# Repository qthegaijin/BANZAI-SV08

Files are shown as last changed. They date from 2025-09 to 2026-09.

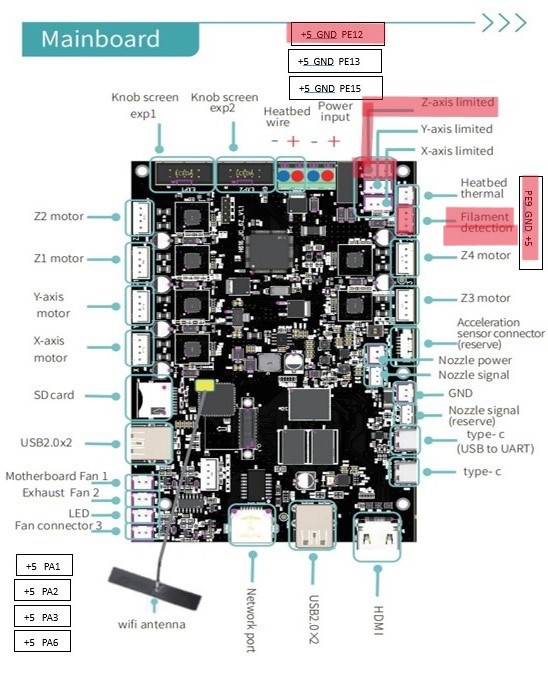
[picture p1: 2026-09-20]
Pinouts/Sovol SV08 MCU_PIN_definition_2 (1).jpg

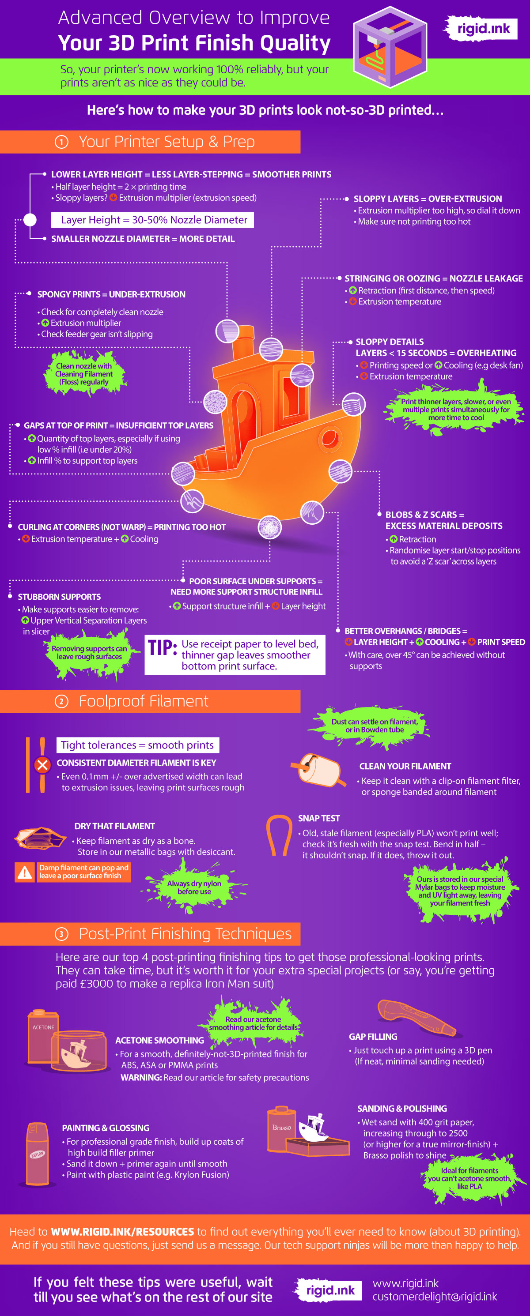
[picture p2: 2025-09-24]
Calibration STLs/Benchy Guide.jpg

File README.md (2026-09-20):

# BANZAI-SV08
Modifications, Configs and Orca Slicer Profiles for the Sovol SV08 3D Printer
<br>
<br>
Model: Sovol SV08 - https://www.sovol3d.com/products/sovol-sv08-3d-printer
<br>
Firmware: Klipper - Mainline - https://github.com/Rappetor/Sovol-SV08-Mainline
<br>
Probe - EddyDuo running eddy-ng - https://github.com/vvuk/eddy-ng/wiki
<br>
KlipperExpander - https://github.com/VoronDesign/Voron-Hardware/tree/master/Klipper_Expander
<br>
Toolhead Cover - Custom Version Coming Soon
<br>
Tophat - https://www.printables.com/model/1392873-sv08-top-hat-double-top-hat-enclosed-for-mmus
<br>
Feet/Risers - https://www.printables.com/model/1041899-sovol-sv08-feet-v4
<br>
Door Stop - https://www.printables.com/model/1003732-sv08-door-stop
<br>
Spool Holder Relocation - https://www.printables.com/model/928589-sovol-sv08-side-mount-spool-holder-remix
<br>
SV08 Gantry Belt Fix - https://www.printables.com/model/1154812-sovol-sv08-side-slide-carriage-make-parallel-to-th
<br>
<br>
Custom SV08 Configs Description -
<br>
eddy-ng.cfg - working config for eddy-ng with updated homing and QGL.
<br>
heatsoak.cfg - variable heatsoak macro
<br>
klipperExpander.cfg - expander board config for Chamber Thermistor
<br>
led-control.cfg - controls toolhead neopixel LED
<br>
printer.cfg - main printer config - use as a reference
<br>
sovol-macros.cfg - updated mainline SV08 Macros
<br>
sovol-stock-purge.cfg - only the purge line macro from the stock sovol setup instead of using KAMP.
<br>
Orbiter2_SmartSensor.cfg - Orbiter Smart Filament Sensor setup for the SV08 on pins PE9 and PE12
<br>
<br>
Custom BANZAI Mods - 
<br>
BANZAI MCU Fan Adapter - Replaces the stock metal sheet cover with a small footprint fan holder. Requres 2 or 4x M3x5mm Heatset Inserts.
<br>

<br>
<br>
BANZAI Bed Plate Mod - Replaces the stock plastic bed plate for use with the SV08 Taco Bed Mod without needing to glue any washers: https://github.com/Wrath669/SV08BedTension/blob/main/README.md. Requires 9 M4x8mm Heatset Inserts.
<br>

<br>

<br>
<br>
Calibration STLs - 
<br>
Suggested Tuning Tutorial Video: https://www.youtube.com/watch?v=trXzdfWCHI8
<br>
Calibration Cube + Key Measuerments Guide - Cube with holes and angled features to measure dimensional accuracy
<br>
Firebolt Calibration - 2A Feature calibration cube "IYKYK"
<br>
Flow Calibration (Depreciated Method, use Built In Orca Calibration Tools instead) - Filament flow calibration square for 0.4MM Nozzles. Print with filament flow ratio at 1.00 to start then measure the walls of the print with calipers. Use the equation 1.20/(Measured Value)*(Flow Rate) to find the desired rate. Repeat steps with new settings applied and remeasure. If walls are > or < 1.20mm redo the equation and rerun the test until you are in the 1.19-1.21mm wall range. 
<br>
<br>
Orca Slicer 2.3.1 Settings -
<br>
<br>
Printer Settings
<br>
SV08-I
<br>
SV08-M
<br>
SV08-E
<br>
SV08-MO
<br>
<br>

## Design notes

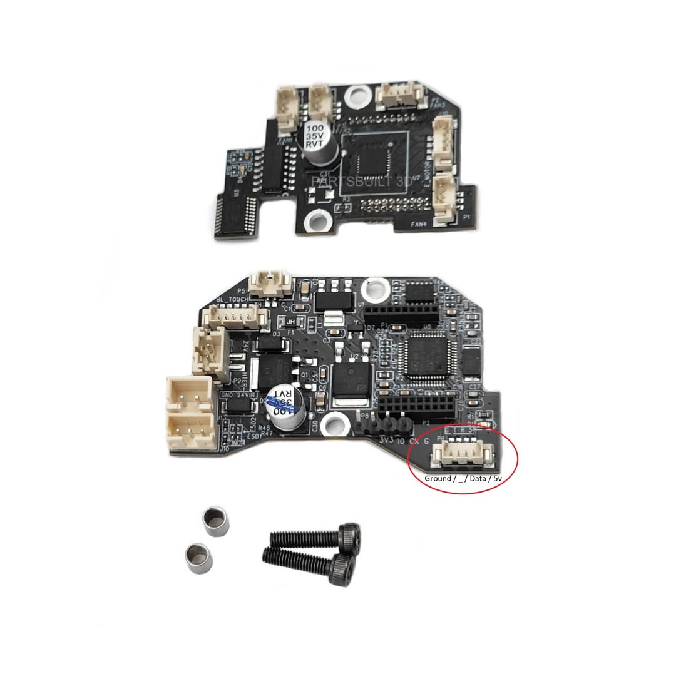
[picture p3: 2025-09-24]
Pinouts/SV08 Toolhead Neo-Pixel Pinout.jpg

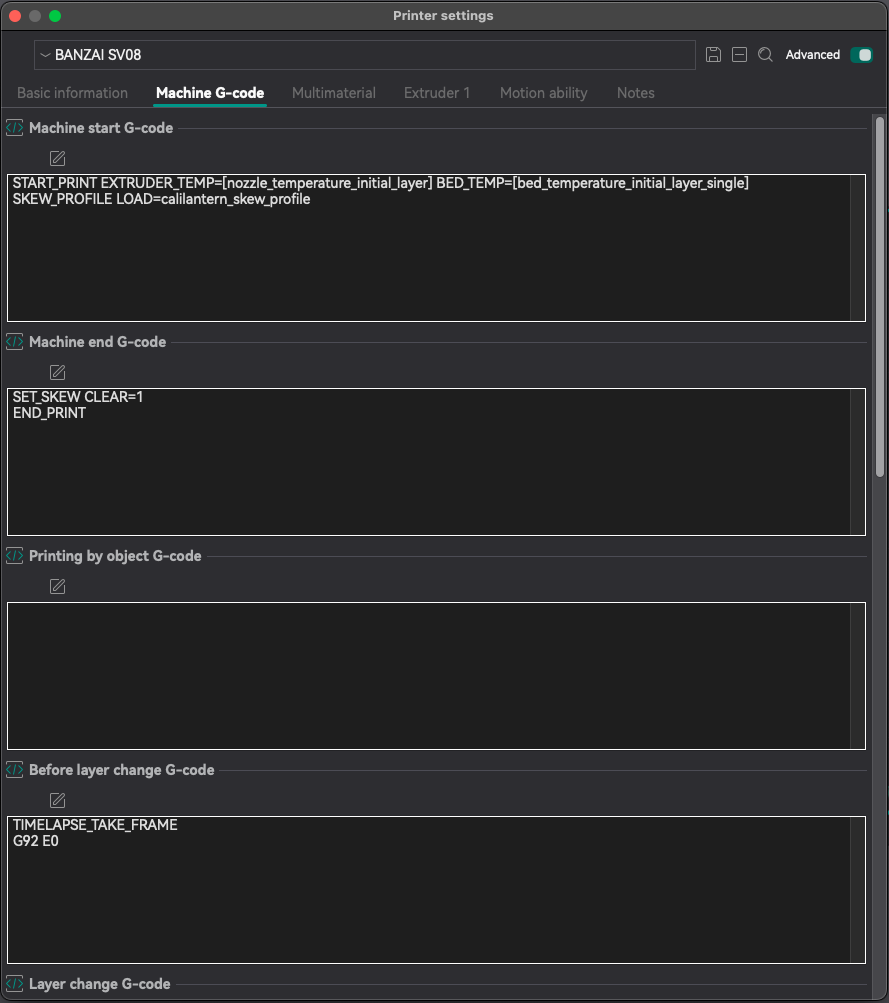
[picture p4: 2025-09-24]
BANZAI SV08 Slicer Images/SV08-M.png

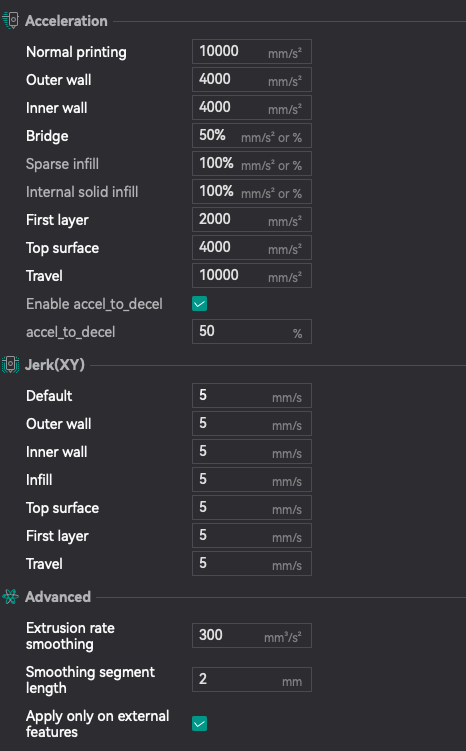
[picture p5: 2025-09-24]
BANZAI SV08 Slicer Images/SP2.png

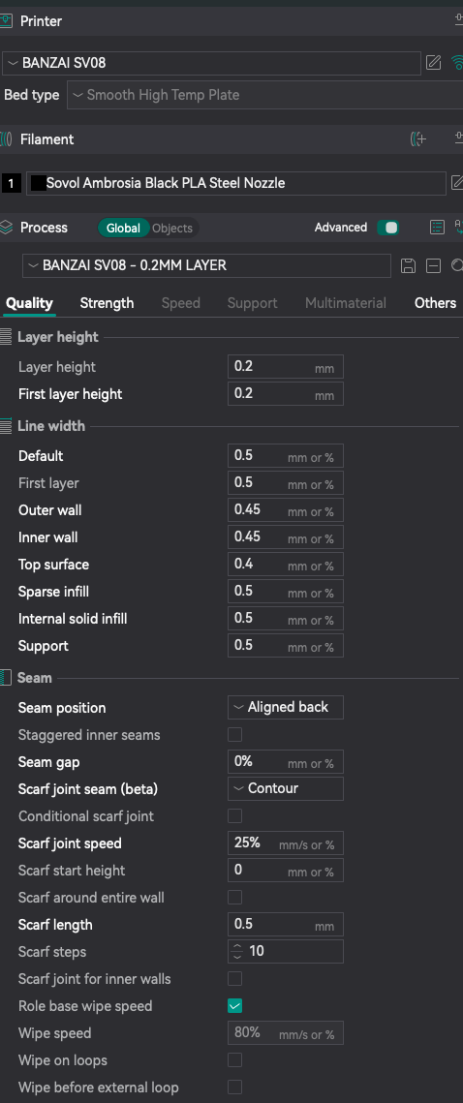
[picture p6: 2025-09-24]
BANZAI SV08 Slicer Images/Q1.png

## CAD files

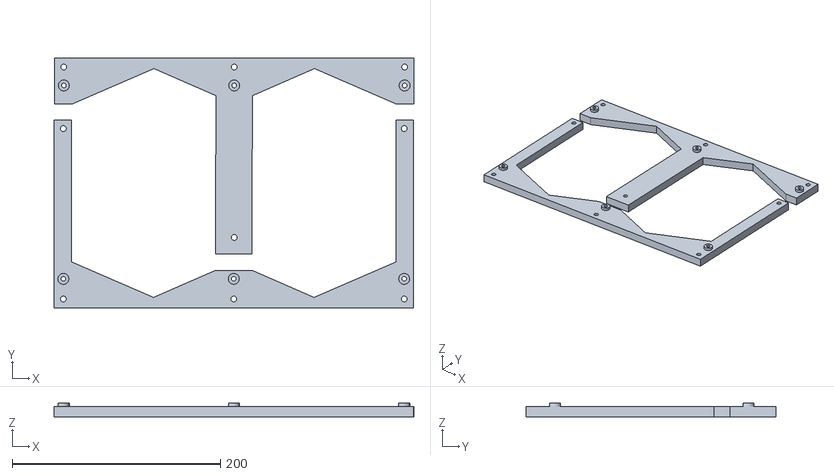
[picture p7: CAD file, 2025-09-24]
BANZAI Custom SV08 Parts/SV08 BANZAI Bed Plate Mod.stl
345.4 x 239.6 x 13.3

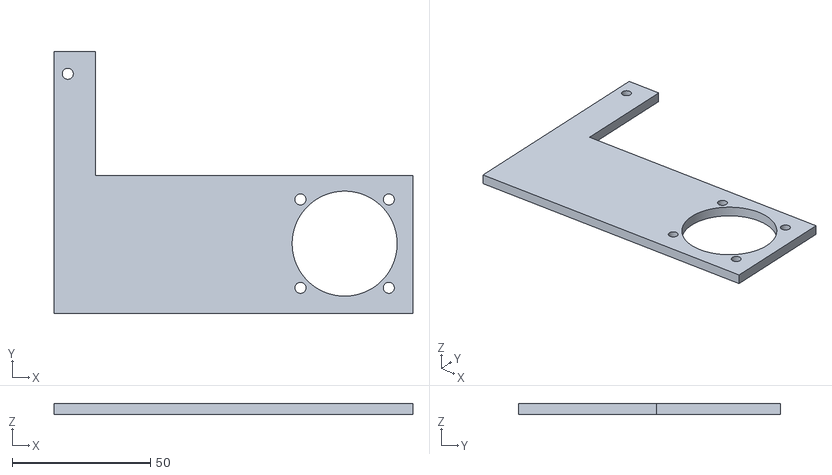
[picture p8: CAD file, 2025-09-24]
BANZAI Custom SV08 Parts/SV08 BANZAI MCU Fan Holder.stl
130.0 x 95.0 x 4.00

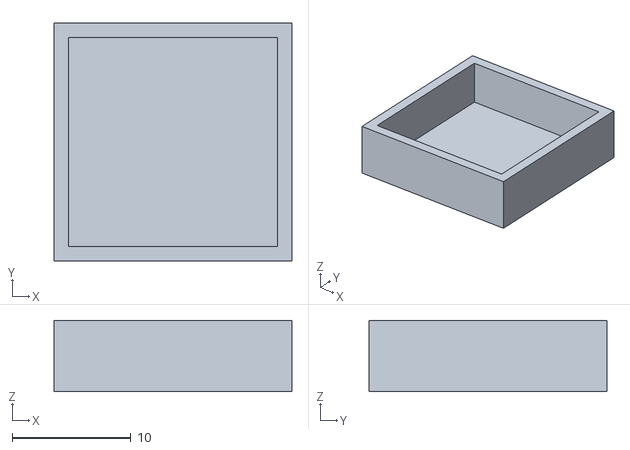
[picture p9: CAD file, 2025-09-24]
Calibration STLs/Flow_Calibration.STL
20.0 x 20.0 x 6.00

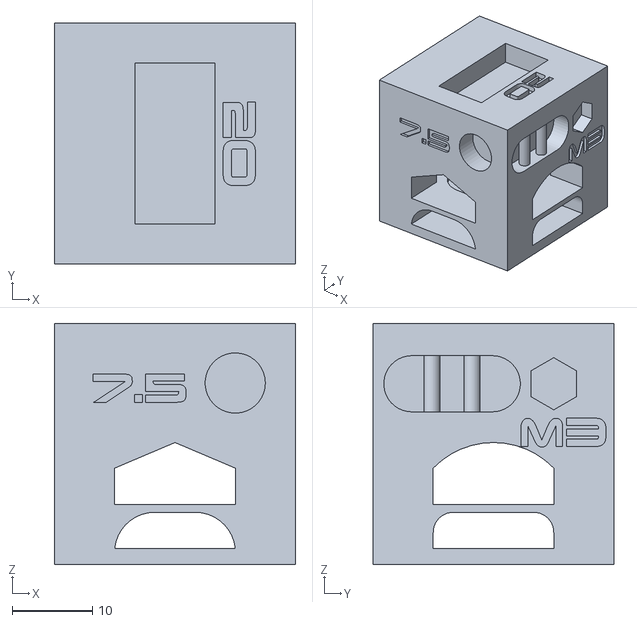
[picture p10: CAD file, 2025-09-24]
Calibration STLs/Calibration_Cube.STL
30.0 x 30.0 x 30.0

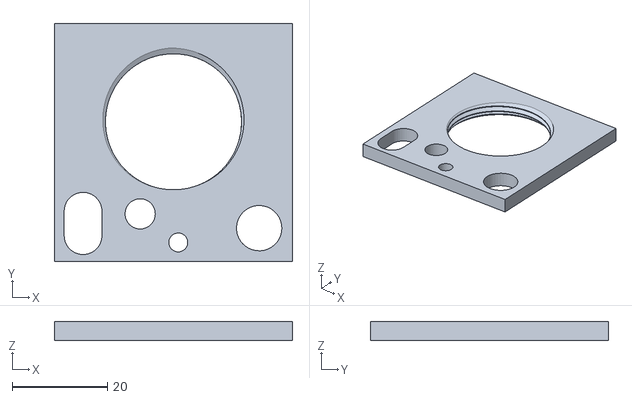
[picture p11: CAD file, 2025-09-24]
Calibration STLs/Firebolt_Calibration_Test.STL
50.0 x 50.0 x 4.00

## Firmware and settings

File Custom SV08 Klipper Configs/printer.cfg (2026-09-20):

[include mainsail.cfg]
[include sovol-macros.cfg]
[include timelapse.cfg] # DONT FORGET TO INSTALL THE TIMELAPSE PLUGIN
[include sovol-stock-purge.cfg]
[include heatsoak.cfg]
[include led-control.cfg]
[include Orbiter2_SmartSensor.cfg]

# PLEASE UNCOMMENT THE FILE THAT BEST FITS YOUR CONFIGURATION

# IF YOU ARE USING THE SCREEN THAT COMES WITH THE SV08
[include options/lcd/*.cfg]

# IF YOU HAVE KLIPPERSCREEN / AN HDMI DISPLAY ATTACHED TO YOUR PRINTER
# [include options/hdmi/*.cfg]

# If you are using the stock probe, keep the following lines as-is.
# If you have an Eddy probe, comment the first and uncomment the second
# [include stock_probe.cfg]
[include eddy-ng.cfg]

# If you are running a Klipper Expander Board
[include klipperExpander.cfg]

# If you will run KAMP Adaptive Purge/Mesh (DOES NOT WORK WITH EDDY_NG)
# [include KAMP_Settings.cfg]


[mcu]
serial: /dev/serial/by-id/usb-Klipper_stm32f103xe_
restart_method: command     

[mcu extra_mcu]
serial: /dev/serial/by-id/usb-Klipper_stm32f103xe_
restart_method: command      

[virtual_sdcard]
path: ~/printer_data/gcodes
on_error_gcode: CANCEL_PRINT

[printer]
kinematics: corexy           
max_velocity: 700            
max_accel: 20000             
#max_accel_to_decel: 10000 # deprecated
minimum_cruise_ratio: 0.5
max_z_velocity: 20
max_z_accel: 500
square_corner_velocity: 6.79

[stepper_x]
step_pin: PE2
dir_pin: !PE0
enable_pin: !PE3
rotation_distance: 40         
microsteps: 64                
full_steps_per_rotation:200   
endstop_pin: tmc2209_stepper_x: virtual_endstop              
position_min: 0 #-1               
position_endstop: 355         
position_max: 355             
homing_speed: 50              
homing_retract_dist: 0        
homing_positive_dir: True     
#--------------------------------------------------------------------
[tmc2209 stepper_x]
uart_pin: PE1
interpolate: False #True             
run_current: 1.1 #1.5
#hold_current: 1.061 #1.5            
sense_resistor: 0.150         
#stealthchop_threshold: 0      
uart_address:3
driver_sgthrs: 75 #65
diag_pin: PE15
driver_TBL: 1
driver_TOFF: 3
driver_HSTRT: 7
driver_HEND: 5

[stepper_y]
step_pin: PB8
dir_pin: !PB6
enable_pin: !PB9
rotation_distance: 40         
microsteps: 64                
full_steps_per_rotation:200   
endstop_pin: tmc2209_stepper_y: virtual_endstop              
position_min: 0 #-1               
position_endstop: 362         
position_max: 362            
homing_speed: 50              
homing_retract_dist: 0        
homing_positive_dir: true     
#--------------------------------------------------------------------
[tmc2209 stepper_y]
uart_pin: PB7
interpolate: False #True             
run_current: 1.1 #1.5
#hold_current: 1.061 #1.5             
sense_resistor: 0.150         
#stealthchop_threshold: 0      
uart_address:3
driver_sgthrs: 85 #75 #65
diag_pin: PE13
driver_TBL: 1
driver_TOFF: 3
driver_HSTRT: 7
driver_HEND: 5

[stepper_z] #motherboard：Z3 
step_pin:PC0    
dir_pin:PE5    
enable_pin:!PC1    
rotation_distance: 40         
gear_ratio: 80:12             
microsteps: 16
endstop_pin: probe:z_virtual_endstop           
position_max: 347             
position_min: -5              
#position_endstop: 0
homing_speed: 15.0
homing_retract_dist: 5.0
homing_retract_speed: 15.0
second_homing_speed: 10.0
#--------------------------------------------------------------------
[tmc2209 stepper_z]
uart_pin: PE6 
interpolate: false #true             
run_current: 0.566 #0.58          
#hold_current: 0.566 #0.58         
sense_resistor: 0.150       
stealthchop_threshold: 999999 
uart_address:3
#driver_TBL: 1
#driver_TOFF: 3
#driver_HSTRT: 0
#driver_HEND: 2

[stepper_z1] ##motherboard：Z1
step_pin:PD3  
dir_pin:!PD1 
enable_pin:!PD4 
rotation_distance: 40         
gear_ratio: 80:12            
microsteps: 64 #16        
#--------------------------------------------------------------------
[tmc2209 stepper_z1]
uart_pin:PD2  
interpolate: false #true             
run_current: 0.566 #0.58          
#hold_current: 0.566 #0.58         
sense_resistor: 0.150  
stealthchop_threshold: 999999 
uart_address:3
#driver_TBL: 1
#driver_TOFF: 3
#driver_HSTRT: 0
#driver_HEND: 2

[stepper_z2] ##motherboard：Z2
step_pin:PD7
dir_pin:PD5   
enable_pin:!PB5
rotation_distance: 40         
gear_ratio: 80:12             
microsteps: 64 #16          
#--------------------------------------------------------------------
[tmc2209 stepper_z2]
uart_pin:PD6  
interpolate: false #true             
run_current: 0.566 #0.58          
#hold_current: 0.566 #0.58         
sense_resistor: 0.150   
stealthchop_threshold: 999999 
uart_address:3
#driver_TBL: 1
#driver_TOFF: 3
#driver_HSTRT: 0
#driver_HEND: 2

[stepper_z3] ##motherboard：Z4
step_pin:PD11 
dir_pin:!PD9 
enable_pin:!PD12   
rotation_distance: 40         
gear_ratio: 80:12             
microsteps: 64 #16       
#--------------------------------------------------------------------
[tmc2209 stepper_z3]
uart_pin:PD10    
interpolate: false #true             
run_current: 0.566 #0.58          
#hold_current: 0.566 #0.58         
sense_resistor: 0.150
stealthchop_threshold: 999999 
uart_address:3
#driver_TBL: 1
#driver_TOFF: 3
#driver_HSTRT: 0
#driver_HEND: 2

[thermistor my_thermistor_e]
temperature1:25
resistance1:110000
temperature2:100
resistance2:7008
temperature3:220
resistance3:435

[extruder]
step_pin: extra_mcu:PA8   
dir_pin: extra_mcu:PB8    
enable_pin:!extra_mcu: PB11   
rotation_distance: 4.69 #6.5 
microsteps: 32 #16                
full_steps_per_rotation: 200 
nozzle_diameter: 0.400        
filament_diameter: 1.75  
max_extrude_only_distance: 500 #150
max_extrude_only_velocity: 120
heater_pin:extra_mcu:PB9  
sensor_type:my_thermistor_e  
pullup_resistor: 11500
sensor_pin: extra_mcu:PA5  
min_temp: 5                  
max_temp: 310                 
max_power: 1.0                
min_extrude_temp: 5
#control : pid
#pid_kp : 33.838
#pid_ki : 5.223
#pid_kd : 47.752
pressure_advance: 0.025       
pressure_advance_smooth_time: 0.035    
#--------------------------------------------------------------------
[tmc2209 extruder]
uart_pin: extra_mcu:PB10  
interpolate: False #True             
run_current: 0.8
#hold_current: #0.8            
uart_address:3
sense_resistor: 0.110 #0.150
stealthchop_threshold: 0
driver_TBL: 0
driver_TOFF: 4
driver_HSTRT: 7
driver_HEND: 6       

[verify_heater extruder]      
max_error: 120                
check_gain_time:30           
hysteresis: 5                
heating_gain: 2               

# [filament_switch_sensor filament_sensor]
# pause_on_runout: True
# event_delay: 3.0
# pause_delay: 0.5
# switch_pin: PE9

#[thermistor my_thermistor]
#temperature1:25
#resistance1:100000
#temperature2:50
#resistance2:18085.4
#temperature3:100
#resistance3:5362.6

[thermistor my_thermistor]
temperature1:25
resistance1:100000
temperature2:75
resistance2:8856.69
temperature3:125
resistance3:3637.10

[heater_bed]
heater_pin:PA0
sensor_type: my_thermistor  
sensor_pin: PC5
max_power: 1.0               
min_temp: 5                  
max_temp: 125                
#control : pid
#pid_kp : 73.571
#pid_ki : 1.820
#pid_kd : 783.849

[verify_heater heater_bed]      
max_error: 120                
check_gain_time:40           
hysteresis: 5                
heating_gain: 2 

# [probe_pressure]
# pin: ^!PE12     
# x_offset: 0                  
# y_offset: 0
# z_offset : 0
# speed: 1.0

[quad_gantry_level]          
gantry_corners:              
	-60,-10
	410,420
points:
	36,10
	36,320
	346,320
	346,10
speed: 300                   
horizontal_move_z: 5       
retry_tolerance: 0.05      
retries: 10                  
max_adjust: 30   

[multi_pin print_cooling_fan_pins]
pins: extra_mcu:PA7, extra_mcu:PB1

# print/part cooling fan
[fan]
pin: multi_pin:print_cooling_fan_pins
max_power: 1.0

[fan_generic exhaust_fan] # exhaust fan
pin: PA2
max_power: 1.0

# MCU fan, aka noisy boi, is now only enabled when using steppers, extruder, heatbed; 5min timeout
[controller_fan MCU_fan]
pin: PA1
max_power: 1
kick_start_time: 0.5
fan_speed: 1
idle_timeout: 300
heater: extruder, heater_bed
stepper: stepper_x, stepper_y
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

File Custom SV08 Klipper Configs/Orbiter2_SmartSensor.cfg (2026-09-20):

#################################################################################################################
################################# Orbiter Sensor CONFIGURATION ##################################################
#################################################################################################################

#config file version v3.0.02
#release date: 22.12.2023

# PAUSE and RESUME macros are defined at the end of this config file.
# If you prefer using your own p[lease delete them, otherwise define parking position below.

#################################################################################################################
################################# CHANGE HERE MACRO CONFIGURABLES################################################
#################################################################################################################

[gcode_macro _SENSOR_VARIABLES]         # change here macro configurables, enable disable functions!*************************
variable_filament_load_temp     :260    # temperature to heat up hotend for filament loading, default is 235
variable_filament_unload_temp   :260    # temperature to heat up hotend for filament un-loading, default is 185
variable_filament_load_min_temp :190    # minimum hotend set temperature allowed in filament load macro, default is 190
variable_nozzle_purge_length    :100    # filament extrude amount during load sequenc, hotend purge from old filament, default is 200
variable_nozzle_purge_speed     :450    # filament extrude speed in mm/min adjust this value lower if flow is too high and extruder skips during loading, default is 300
variable_unload_distance        :65     # filament retract distance for unload procedure. this length shall be long enough to extract the filament above the drive gears
variable_disable_autoload       :False  # disable filament autoload feature by setting this variable True
variable_disable_runnout        :False  # disable runnout by setting this variable True
variable_disable_autochange     :False  # disable filament auto change after runnout detection
variable_disable_tangle         :False  # disable tangle by setting this variable True
variable_disable_autounload     :False  # disable auto unload filament by setting this variable to True
variable_enable_beep            :False  # uses M300 sound feature, set it True to enable
variable_park_position_x        :10     # edit your X parking position here for pause macro trigerred by runnout
variable_park_position_y        :10     # edit your Y parking position here for pause macro trigerred by runnout
variable_park_lift_z            :10     # edit your Z lift amount for parking position here, default is 10
Variable_park_retraction        :1      # edit your retraction amount for parking, default is 1
gcode:


#///////////////////////////filament sensor button macros/////////////////////////////////////////////////
#[gcode_button filament_sense]
#pin: !orbitoolO2:PA9 # remove the negation "!" for sensor v1 - use just PA9 as example
#pin: !orbitoolO2:PA13 # remove the negation "!" for sensor v1 - use just PA9 as example
#press_gcode: # sensor released  -runnout detected!
 
#release_gcode: #gcode macro for filament auto-load, sensor pressed
  #filament_load_init

[filament_switch_sensor filament_sensor]
switch_pin: PE9
pause_on_runout: True
runout_gcode: runnout_init
insert_gcode: filament_load_init
event_delay: 3.0
pause_delay: 0.5

#********************************************************************************************************

#////////////////////////////////////////Filament Unload macros/////////////////////////////////////////////////
[gcode_button filament_unload]
pin: PE12 # remove the negation "!" for sensor v1 - use just PA9 as example
press_gcode:  # filament unload procedure   
  unload_tangle_init
release_gcode: # do not add any macro call here

#################################################################################################################################
####################################### DO NOT CHANGE ANYTHING BELOW THIS LINE!!! ###############################################
#################################################################################################################################
####################################### UNLESS YOU KNOW WHAT YOU ARE DOING OR YOU ARE BORED AND NEED TO DO SOMETHING OR YOU ARE ALONE AND NEED SOMETHING TO MESS UP YOUR LIFE OR YOU CAN DO IT BETTER THAN ME OR YOU ARE A REAL SMARTASS OR JUST BECAUSE YOU CAN OR YOU RUN OUT OF BEAR OR HAS NOTHING BETTER TO DO OR ANY UNREASONABLE REASON
#################################################################################################################################

[respond]
default_type: echo

# [force_move]
# enable_force_move: True

[gcode_macro runnout_init]
gcode:
  {% set sensor = printer['gcode_macro _SENSOR_VARIABLES'] %}  
  {% if(sensor.disable_runnout|lower == 'false') %}
      filament_change_state1
  {% else %}
    M118 Filament runnout is disabled in the sensor config file!   
  {% endif %} 

[gcode_macro filament_change_state1]
variable_changebusy: 0
variable_temp_target: 0
gcode:
  {% set sensor = printer['gcode_macro _SENSOR_VARIABLES'] %}  
  {% if changebusy == 0 %}
    PAUSE # call printer pause macro          
    M118 Filament runnout!       
    {% if (sensor.disable_autochange|lower == 'false') %}
      SET_GCODE_VARIABLE MACRO=filament_change_state1 VARIABLE=changebusy VALUE=1       
      filament_change_state2   # comment this line if you do not want to automatically unload filament in case there is a runnout detected.
    {% endif %}  
  {% endif %}

[gcode_macro filament_change_state2]
gcode:
  {% set sensor = printer['gcode_macro _SENSOR_VARIABLES'] %}  
  SET_GCODE_VARIABLE MACRO=unload_tangle_init VARIABLE=loadbusy VALUE=1  
  {% if (sensor.enable_beep|lower == 'true') %} 
    M300 # beep sound
  {% endif %}
  M118 Unloading filament...   
  M83
  G92 E0   
  # {% if printer[printer.toolhead.extruder].temperature < 185 %} # hardcoded threshold
  {% if (printer.extruder.can_extrude|lower != 'true')%} # checing for minimum extrusion temperature
        # check if temperature is over the minimum extrusion temp. min_extrude_temp must be defined in the extruder config (to about 185)
      M118 Hotend heating!        
      SET_HEATER_TEMPERATURE HEATER=extruder TARGET={sensor.filament_unload_temp} # restore user temp if it was set before loading
      TEMPERATURE_WAIT SENSOR=extruder MINIMUM={sensor.filament_unload_temp} #wait for reaching filament unload temp
      {% endif %}     
  {% if(printer.extruder.target == 0) %} # checing for set temperature if is zero than set to 200 / hotend hot but cooling due to set target temp 0
      SET_HEATER_TEMPERATURE HEATER=extruder TARGET={sensor.filament_unload_temp} # restore user temp if it was set before loading
      TEMPERATURE_WAIT SENSOR=extruder MINIMUM={sensor.filament_unload_temp} #wait for reaching filament unload temp
  {% endif %} 
  G0 E-5 F3600 	#extract filament to cold end
  G4 P2000 # wait for two seconds
  G0 E5 F3600 # push the filament back 
  G0 E-5 F3600 	#extract filament to cold end
  G0 E-{sensor.unload_distance} F300	# continue extraction slow allow filament to be cooled enough before reaches the gears  
  M400   
  M118 Load new filament! Wait until is loaded, then resume printing.  
  SET_HEATER_TEMPERATURE HEATER=extruder TARGET=0 # swicth off heater
  UPDATE_DELAYED_GCODE ID=clear_loadbusy DURATION=0.5
  UPDATE_DELAYED_GCODE ID=clear_changebusy DURATION=0.5

[gcode_macro filament_load_init]
gcode:
  {% set sensor = printer['gcode_macro _SENSOR_VARIABLES'] %}
  {% if (printer.print_stats.state != "printing") %}
    {% if(sensor.disable_autoload|lower == 'false') %}
      SET_GCODE_VARIABLE MACRO=unload_tangle_init VARIABLE=loadbusy VALUE=1
      filament_load
    {% else %}
    M118 Filament auto-load is disabled in the sensor config file!   
    {% endif %} 
  {% else %}    
    M118 Printing! Can't load filament right now!    
  {% endif %} 
 # SET_GCODE_VARIABLE MACRO=filament_unload VARIABLE=filamentpresent VALUE=1
  #UPDATE_DELAYED_GCODE ID=clear_changebusy DURATION=2
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
